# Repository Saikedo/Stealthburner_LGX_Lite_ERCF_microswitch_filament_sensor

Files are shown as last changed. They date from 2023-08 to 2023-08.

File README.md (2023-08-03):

# Stealthburner CW2 LGX Lite Mount with Microswitch Filament Sensor for ERCF

**Note:** The original idea and base CAD models originated from the repository [LGX_Lite_Stealthburner_CW2_style_mount](https://github.com/Eytecz/LGX_Lite_Stealthburner_CW2_style_mount/tree/main). After several unsuccessful attempts to integrate it with a hall effect sensor (which repeatedly failed after a few days), I decided to create a mount that employs a microswitch. I'll provide instructions for mounting the microswitch; however, for detailed assembly instructions, you should refer to the aforementioned repository.

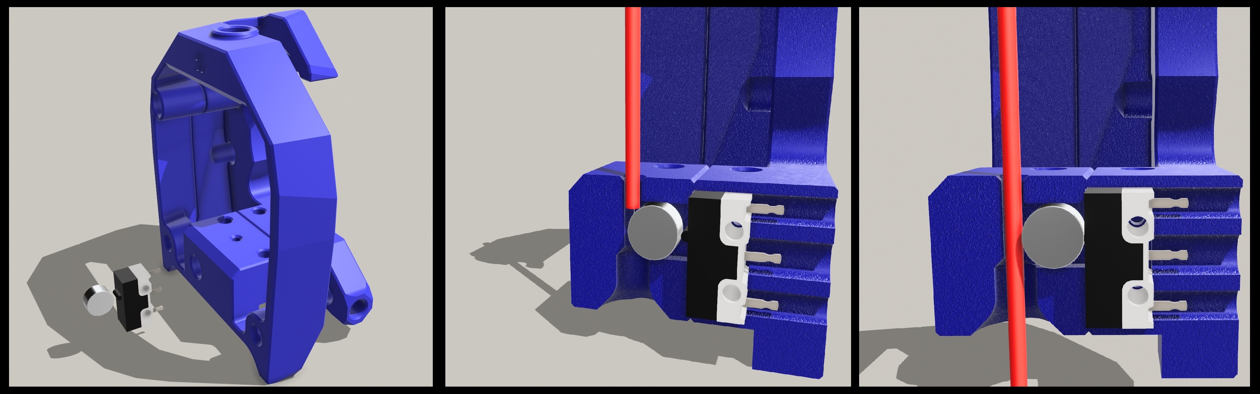
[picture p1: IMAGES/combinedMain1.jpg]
Main Image


The filament sensor requires two components:

* D2F-01L Switch (Other switches with similar dimensions should work just fine)
* 6x3mm magnet (You don't actually require a magnet; anything with dimensions of 6mmx3mm should suffice). It's crucial to have the cylinder's radius as close to 6mm as possible. The height doesn't need to be as precise, but aim for less than 3mm.

# Printing Instructions
For printing, utilize the default Voron parts printing settings. There's no need for additional supports or alterations in settings.

# Assembly Instructions and Tips

# Step 1: Magnet Insertion
Insert the magnet into the magnet hole in the Front_body_LGX_Lite_Stealthburner_ERCF. Ensure that the magnet can move freely within the hole and encounters no resistance. The magnet should protrude into the filament hole by about 1.25mm.

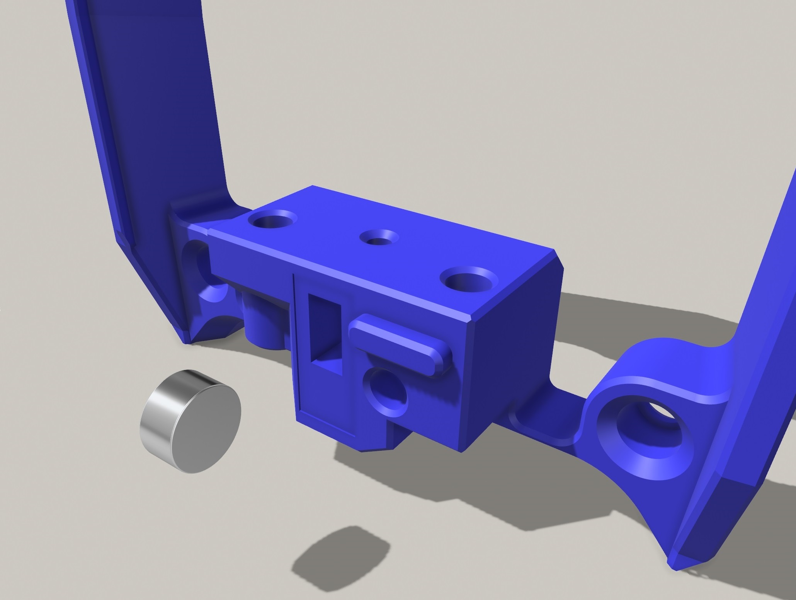
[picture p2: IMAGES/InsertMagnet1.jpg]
Insert magnet instruction photo
 

# Step 2: Button Wiring
Solder two wires to the button and feed the wires through the holes at the back of the button hole in the Rear_body_LGX_Lite_Stealthburner_ERCF part. I will discuss my personal wiring preferences at the end of this document.

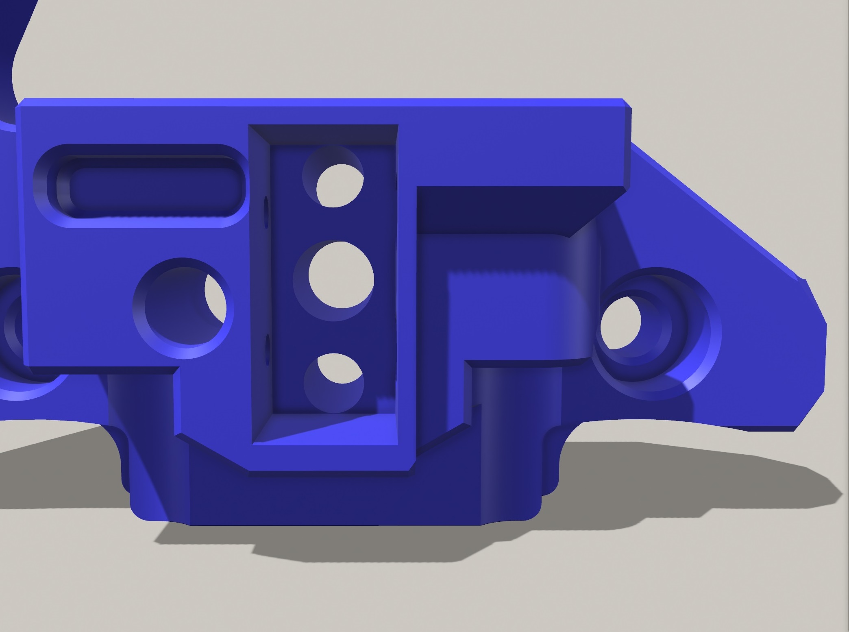
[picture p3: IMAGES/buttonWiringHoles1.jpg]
Button wiring instruction photo
 

# Step 3: Button Insertion
Begin inserting the button into the Rear_body_LGX_Lite_Stealthburner_ERCF part. It might be a tight fit and require some force to fully insert, but make sure that it goes all the way in. After insertion, the button should protrude by about 0.75mm from the front.

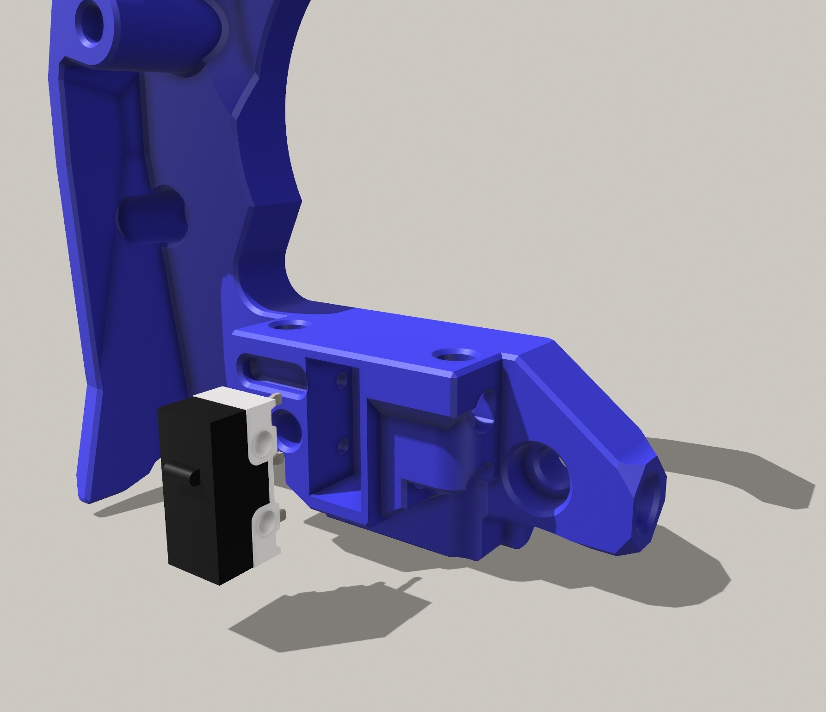
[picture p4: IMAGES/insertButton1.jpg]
Button insertion instruction photo
 

# Step 4: Self Tapping Screws (Optional)
I designed holes in the Rear_body_LGX_Lite_Stealthburner_ERCF to enable screwing in the button with M2x8mm self-tapping screws. I personally used [these screws](https://www.amazon.com/gp/product/B00YBMRAH4/ref=ppx_yo_dt_b_search_asin_title?ie=UTF8&th=1). Note, however, that this step should be optional since the button should already be snugly fitted into the part and will later be sandwiched between the two parts. Despite this, I conducted all my testing with the screws, so proceed without them at your own risk.

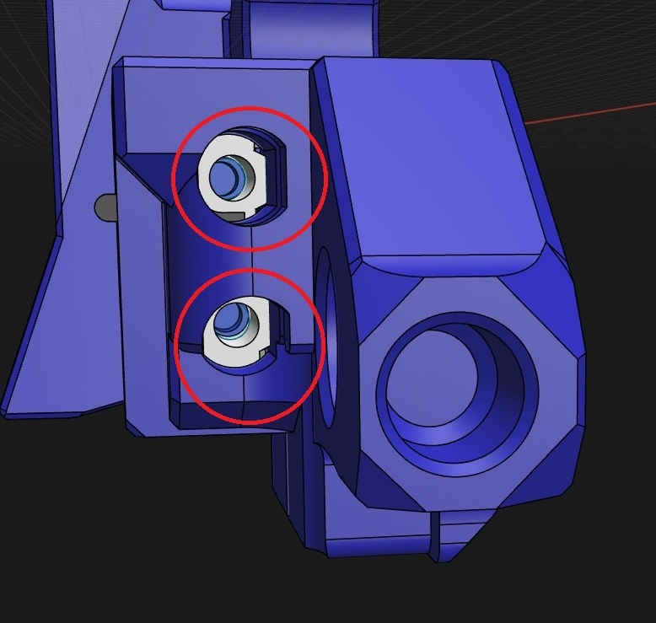
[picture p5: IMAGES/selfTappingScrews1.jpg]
Self tapping screws instruction photo
 

# Step 5: Initial Testing
Position the two parts together and hold them firmly. Insert a filament into the filament hole and listen for a clicking sound from the button when inserting the filament. Verify that the button is properly unclicking when removing the filament.

# Button Wiring
The Rear_body_LGX_Lite_Stealthburner_ERCF part features holes for all three prongs of the button, so you can wire it in any way you prefer. Below is my personal wiring method.

I wired the button in a normally open position (no voltage if the button isn't pressed). With this setup, the filament sensor will report no filament if the sensor wires aren't connected or if there are any issues with the wiring. I personally use the EBB36 (Version 1.2) canBus board, so the diagram below demonstrates wiring to the EBB36 board, but you can connect this to any other pin as well.

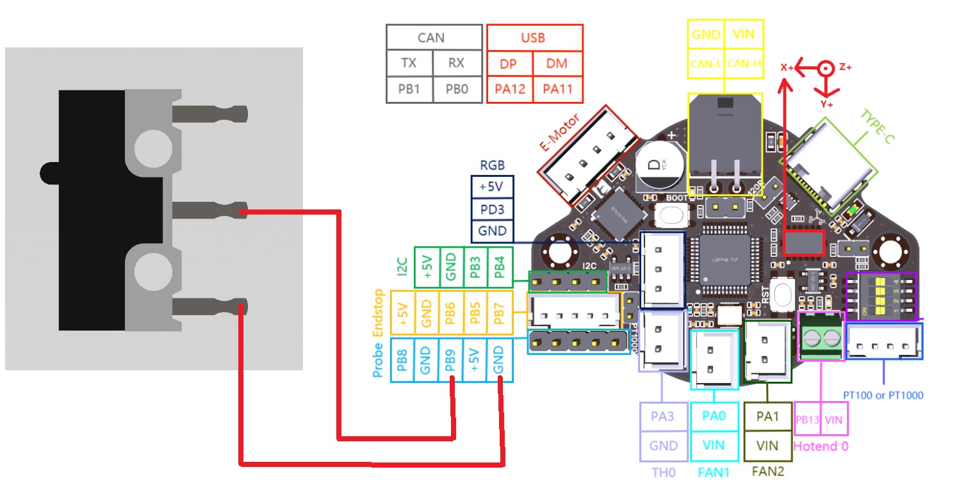
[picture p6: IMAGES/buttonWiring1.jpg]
Button wiring instruction photo
 

Use the following Klipper code for ERCF (place this in ercf_hardware.cfg):

```
[filament_switch_sensor toolhead_sensor]
pause_on_runout: False		# Must be False
switch_pin: ^!YOUR_PIN  # If you have EBB36 and wired it similarly to the diagram above, this line will be switch_pin: ^!EBBCan:PB9
```

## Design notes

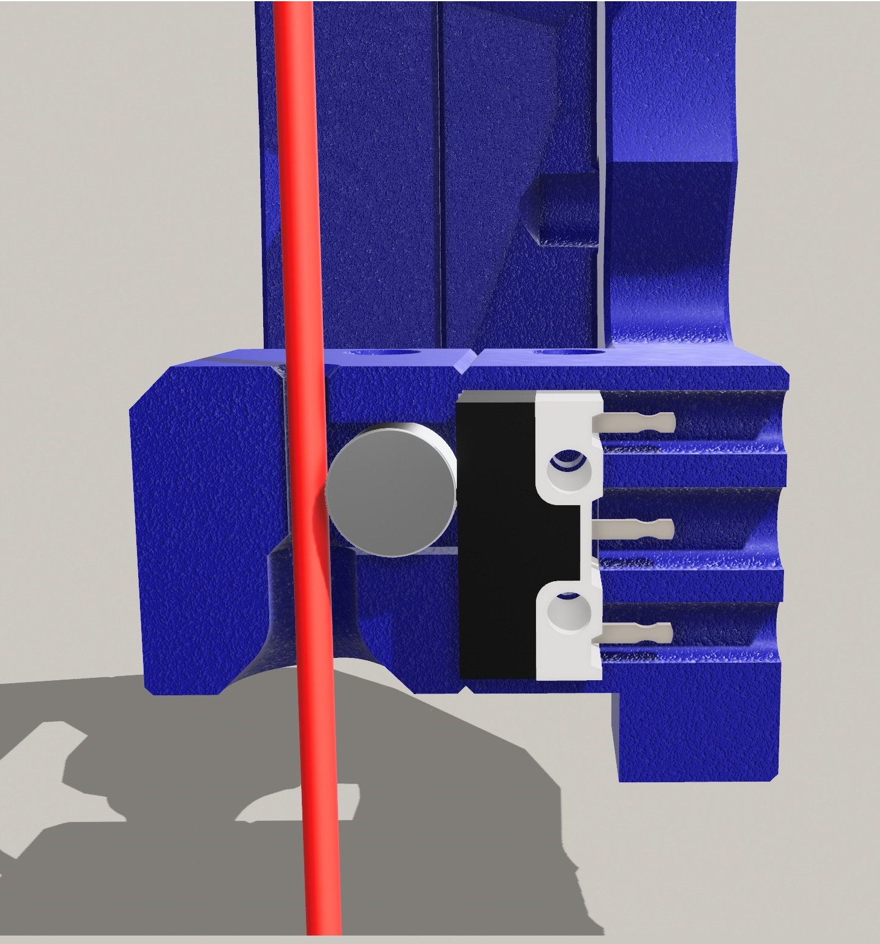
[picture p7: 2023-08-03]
IMAGES/filamentAfter1.jpg

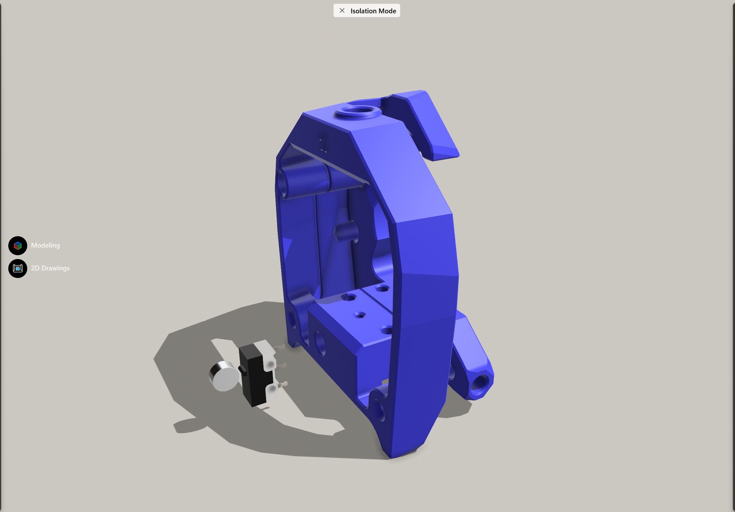
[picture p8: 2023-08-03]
IMAGES/mainImage1.jpg

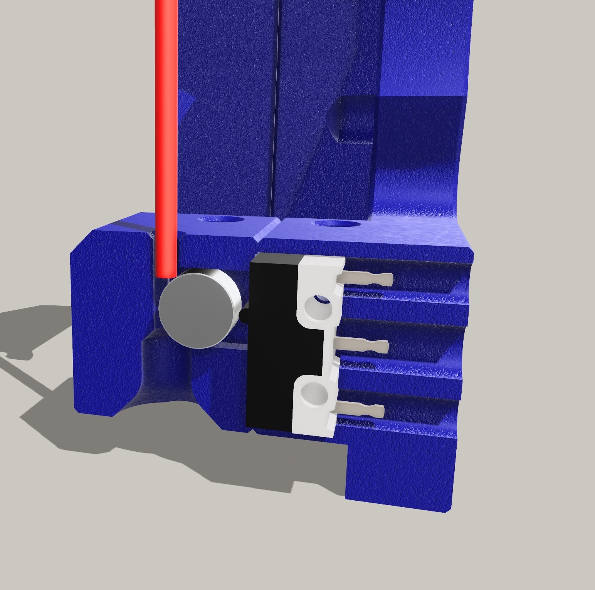
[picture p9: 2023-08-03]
IMAGES/filamentBefore1.jpg

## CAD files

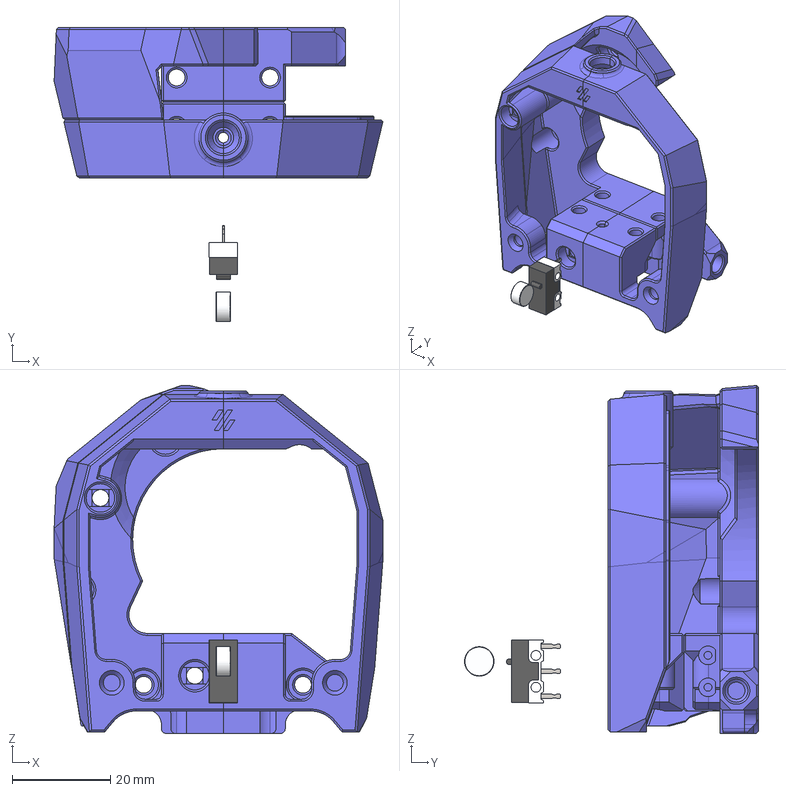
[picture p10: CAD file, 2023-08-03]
STEP/Stealthburner_LGX_Lite_ERCF_microswitch_filament_sensor.step
66.9 x 59.8 x 70.8 mm
Rear_body_LGX_Lite_Stealthburner_ERCF_Released_rev01
Front_body_LGX_Lite_Stealthburner_ERCF_Released_rev01
switch

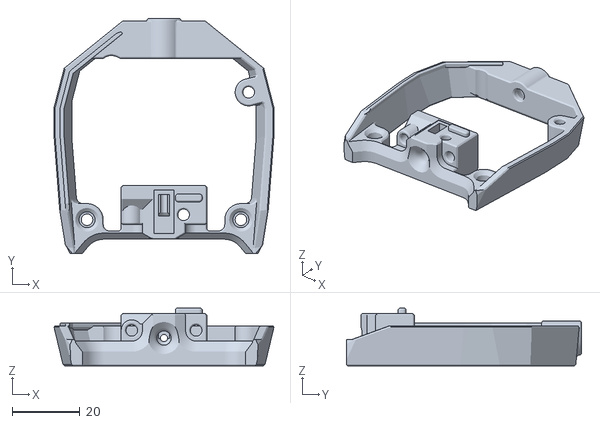
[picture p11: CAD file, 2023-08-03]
STL/Front_body_LGX_Lite_Stealthburner_ERCF.stl
64.9 x 69.4 x 17.0

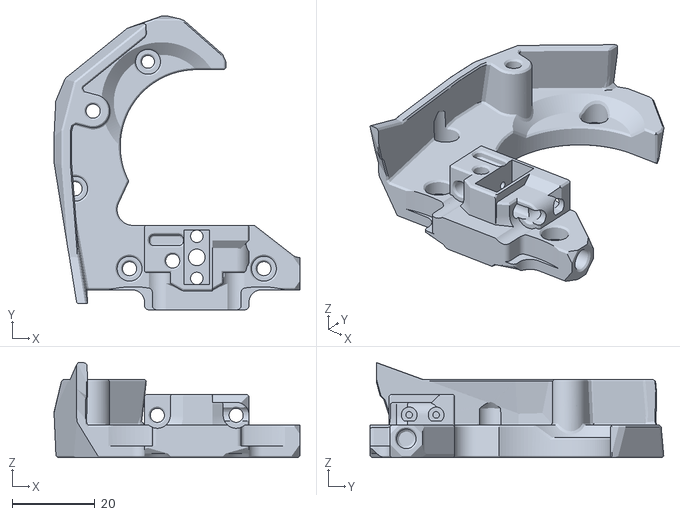
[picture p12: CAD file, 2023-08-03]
STL/Rear_body_LGX_Lite_Stealthburner_ERCF.stl
59.3 x 70.8 x 22.9

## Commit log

2023-08-03 Adding step and stl files
    [Front_body_LGX_Lite_Stealthburner_ERCF.stl, Rear_body_LGX_Lite_Stealthburner_ERCF.stl]
2023-08-03 Fixing stls
    [Front_body_LGX_Lite_Stealthburner_ERCF.stl, Rear_body_LGX_Lite_Stealthburner_ERCF.stl]
2023-08-03 Added the proper step file
    [Stealthburner_LGX_Lite_ERCF_microswitch_filament_sensor.step]
